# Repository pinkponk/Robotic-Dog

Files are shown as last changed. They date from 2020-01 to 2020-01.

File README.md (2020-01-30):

# Robtic-Dog
A robotic dog capable of walking using 12 robotic servos, an Arduino and a lot of 3D printing. The servos had position feedback and torque control. The onboard arduino mega board talked to the servos through a custom communication curcuit. All the servos used a communication bus which made it possible to daisy chain the communication. The power was drawn from an onboard battery through a dcdc converter to regulate the voltage. It was planned for the robot to use 2 more servos as the spine but there was not enough time to add control code for these 2 servos, the spine was made stiff. The robot did managed to walk but due to the high latency communication, the low resolution position feedback and the time limit it was too difficult to make a dynamic gait work well.

# Documentation
Read the report in the docs dir if you want to know more.

Robot CAD                  |  Target gait
:---------------------------:|:---------------------------------------------:
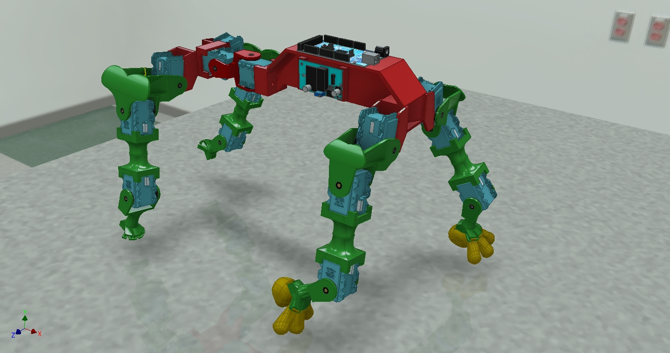
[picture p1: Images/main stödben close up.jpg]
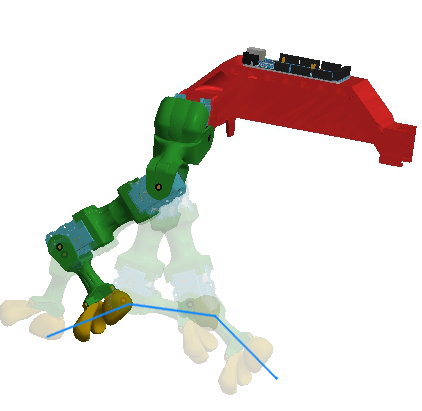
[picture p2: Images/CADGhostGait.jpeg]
  |  

Complete robot                  |  Matlab simulation of gait and inverse kinematics
:---------------------------:|:---------------------------------------------:
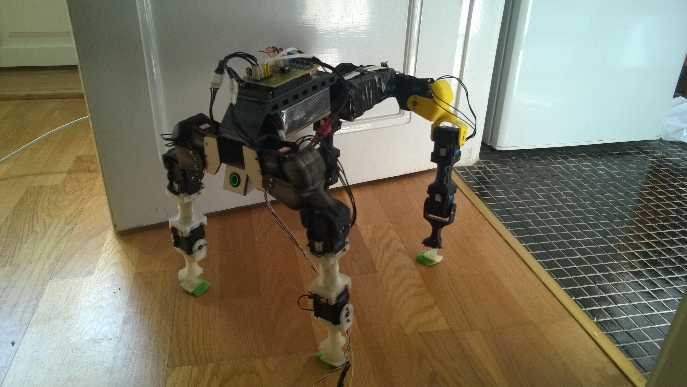
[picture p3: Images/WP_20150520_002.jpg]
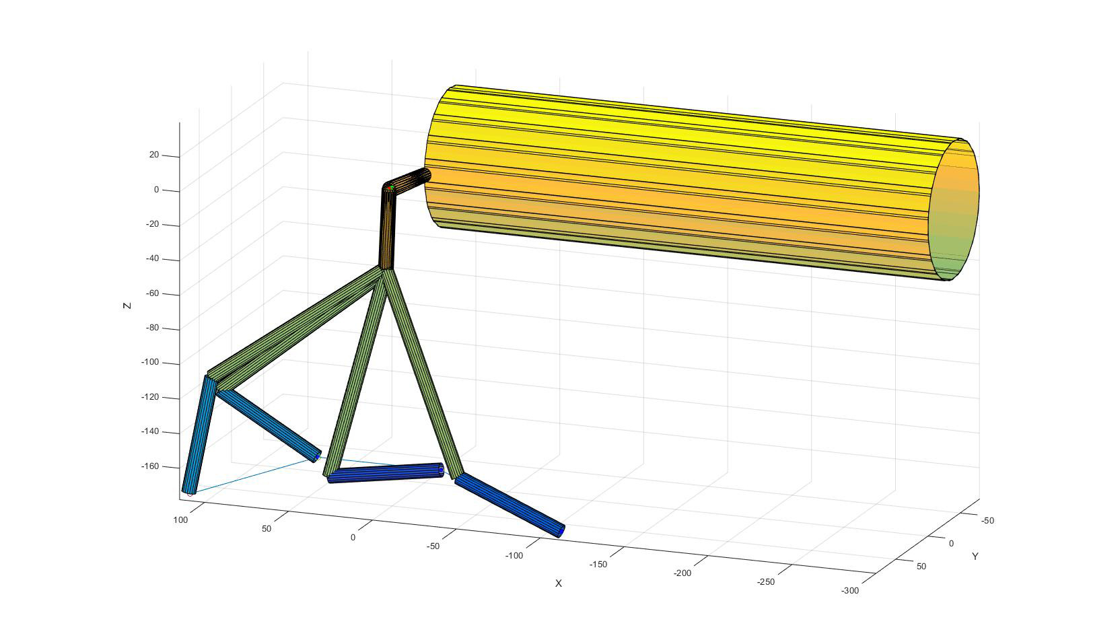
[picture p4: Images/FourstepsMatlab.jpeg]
 | 

Calculating Inverse kinematics                  |  Calculating Inverse kinematics
:---------------------------:|:---------------------------------------------:
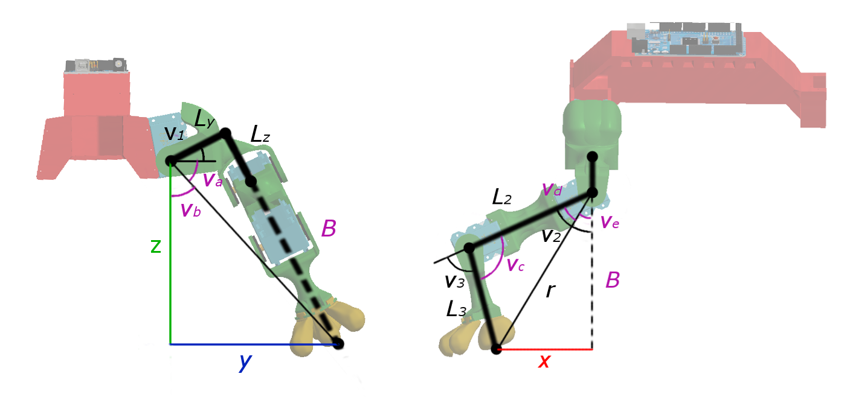
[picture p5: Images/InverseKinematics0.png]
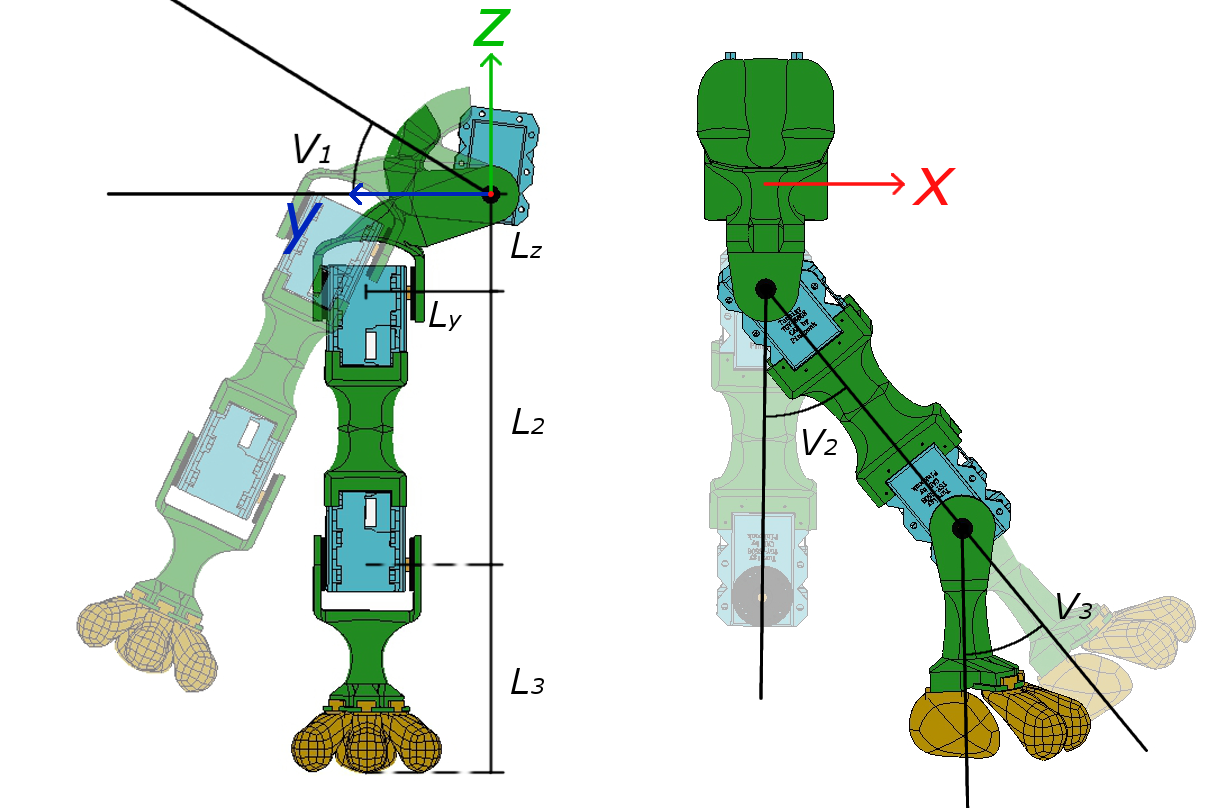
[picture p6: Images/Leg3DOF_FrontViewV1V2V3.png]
  |

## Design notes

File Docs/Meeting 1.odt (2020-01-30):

# Meeting 1

Mitt arbete bygger runt vilket servo jag använder mig av. Jag har beställt ett:

http://hobbyking.com/hobbyking/store/__41216__Turnigy_TGY_S508_300_Digital_Intelligent_Metal_Gear_Robot_Servo_8kg_0_16Sec_75g.html

It has arrived in here in Sweden yesterday so I will begin testing next week. When I actually have the servo and can confirm that it will work with my project I will order the rest. The dimensions given are a bit on the fusy side so I will make the messurment myself when I get the actuall piece. I will probebly have to build some connectors by myself but the majority will be bought, for example like this one:

http://www.ebay.com/itm/131270241221?_trksid=p2055119.m1438.l2649&ssPageName=STRK%3AMEBIDX%3AIT (http://www.ebay.com/itm/131270241221?_trksid=p2055119.m1438.l2649&ssPageName=STRK%3AMEBIDX%3AIT)

I have emailed the buyer I gotten the dimensions needed for this piece but again I will have to check with the actual servo I bought.

To power the servos I will use a battery I already have (12V) I will need some power electronics given that the servos run on 7,6 V. Like this one:

http://www.ebay.com/itm/2PCS-LM317-DC-DC-Converters-Buck-Power-Module-Adjustable-Linear-Regulator-/361095746885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

I will also implement some cheap pressure sensors on each fot, maybe not for a start but later on these will become valuble info:

http://www.ebay.com/itm/0-40kPa-MPS20N0040D-D-DIP-6-Sphygmomanometer-Pressure-Sensor-/331477178244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

Every cool robot needs a sexy power switch:

http://www.ebay.com/itm/16mm-Red-Start-Horn-Button-Momentary-Stainless-Steel-Metal-Push-Button-Switch-/331476329256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

Also some cute eye's:

http://www.ebay.com/itm/MAX7219-Dot-Matrix-Module-Control-Display-Module-DIY-kit-Cascade-uk-/361102115385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

Budget for phase 1:

6 servos = 1284 SEK

6 mounting brackets = 176 SEK

2 DC-DC step down= 24 SEK

2 pressure sensors = 32 SEK

1 power switch = 25 SEK

2 eye's = 52 SEK

Tot = 1600 SEK

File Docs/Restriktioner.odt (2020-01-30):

En motor bör klara av att lyfta halva vikten av roboten => maximal längd för ben

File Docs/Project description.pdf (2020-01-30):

Henrik Ljunggren
2015-02-01

# Quadruped with spine

Project description
I will make a Quadruped, a four legged robot with a spine. The robot will be able to walk using a pre-programmed pattern in phase one and will tech itself how to walk in phase two.

Engineering problem
The foremost problem lays with using ordinary servos. With normal servos no feedback is available and so one never knows the actual location of the leg/arm, making building a walking robot/running robot hard. I will therefore use special servos which can transmit [angle, angle speed, temp and more] back to the controller. These special servos communicate using CAN-bus and are connected in series.

Research question
Phase One: How will a gait with the use of a spine compare with not using a spine? Phase Two: How does a pre-programmed gait/walk compare to a self learned gait/walk?

Components
For phase one I will need, depending on the structural design a lot of special servos around 12-14 and one CAN-bus shield for arduino. I will also need many structural connectors to attach the servos to one and other.
For phase Two I will need som sort of balancing sensor.

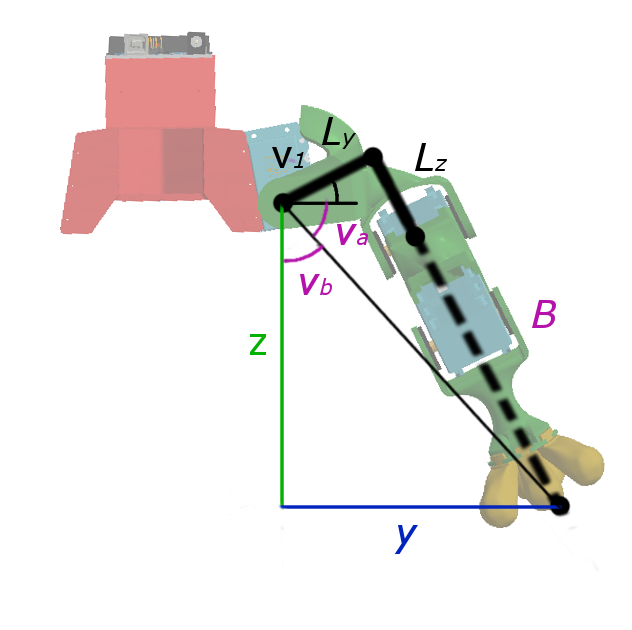
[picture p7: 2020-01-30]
Images/InverseKinematics1.png

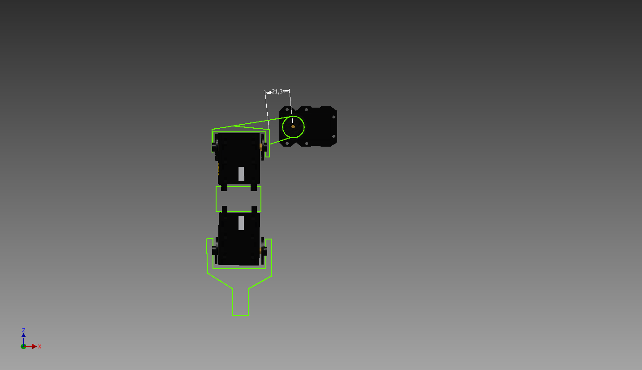
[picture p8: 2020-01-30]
Images/Leg3DOFOverallDesign.bmp

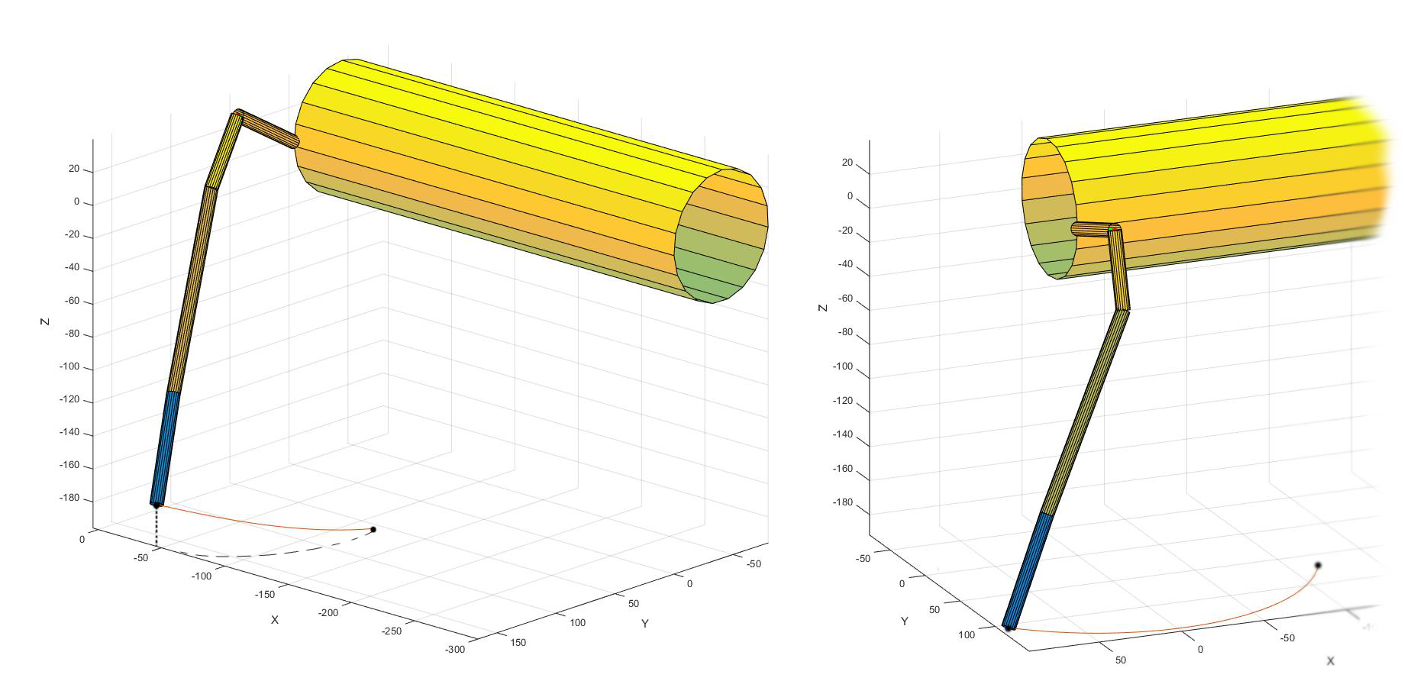
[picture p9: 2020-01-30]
Images/2DoFTransportandSupport.png

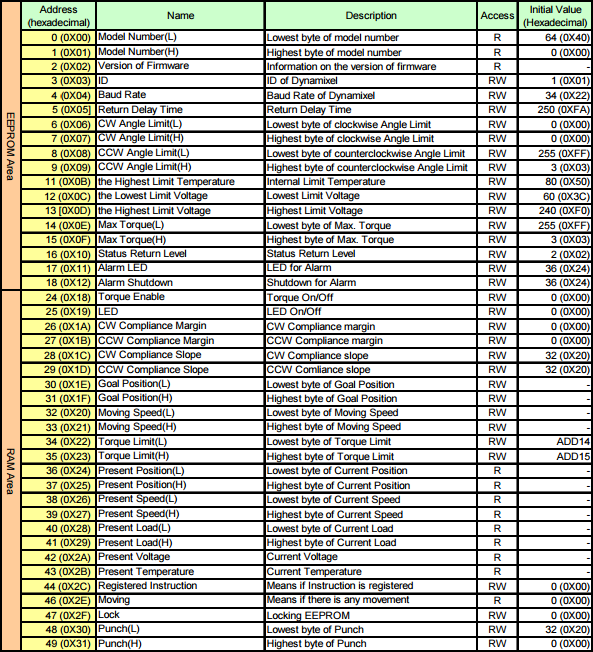
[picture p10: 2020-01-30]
Docs/SR518 servo/ControlTable.png

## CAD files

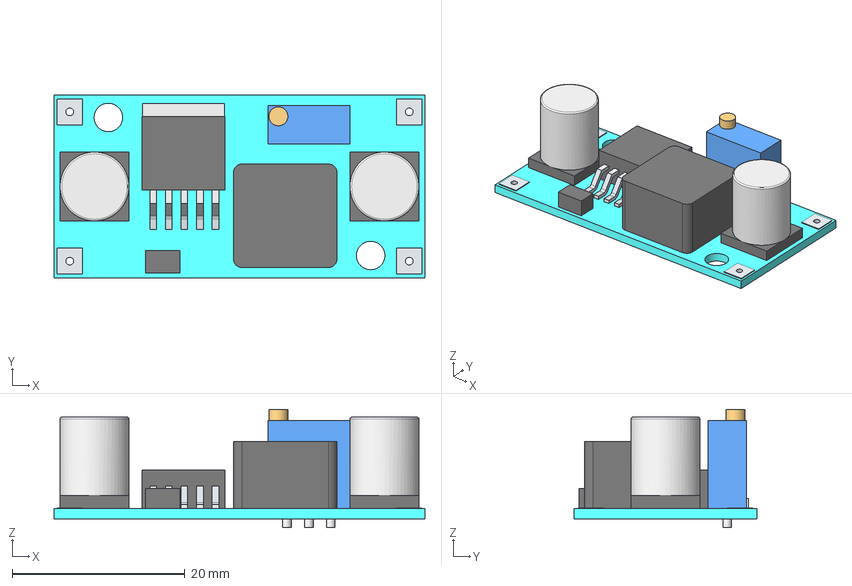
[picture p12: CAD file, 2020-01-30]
CAD/DCDCStepDown/Step Down voltage regulator LM2596.stp
43.0 x 21.2 x 13.7 mm

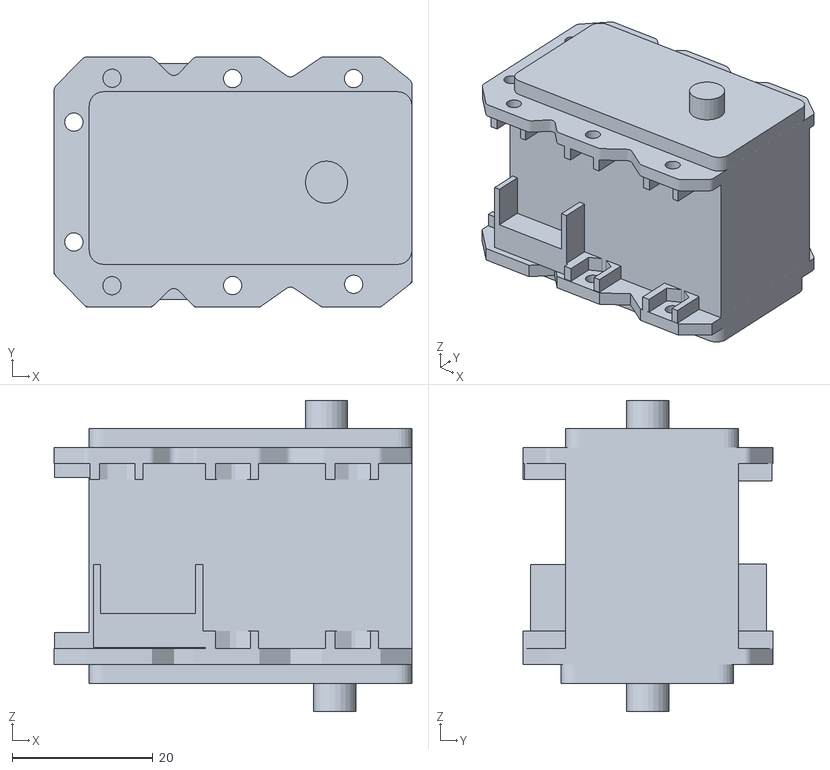
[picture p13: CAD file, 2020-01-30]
Docs/SR518 servo/CAD_SR518 servo/1832732_SR518 servo/SR518 servo.stl
50.8 x 35.5 x 44.1

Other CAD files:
CAD/Arduino Mega 2560/Assembly1.iam
CAD/Arduino Mega 2560/PCB-FIXED.ipt
CAD/Arduino Mega 2560/Part10.ipt
CAD/Arduino Mega 2560/Part12.ipt
CAD/Arduino Mega 2560/Part14.ipt
CAD/Arduino Mega 2560/Part16.ipt
CAD/Arduino Mega 2560/Part18.ipt
CAD/Arduino Mega 2560/Part20.ipt
CAD/Arduino Mega 2560/Part22.ipt
CAD/Arduino Mega 2560/Part24.ipt
CAD/Arduino Mega 2560/Part26.ipt
CAD/Arduino Mega 2560/Part28.ipt
CAD/Arduino Mega 2560/Part30.ipt
CAD/Arduino Mega 2560/Part32.ipt
CAD/Arduino Mega 2560/Part34.ipt
CAD/Arduino Mega 2560/Part36.ipt
CAD/Arduino Mega 2560/Part38.ipt
CAD/Arduino Mega 2560/Part4.ipt
CAD/Arduino Mega 2560/Part40.ipt
CAD/Arduino Mega 2560/Part42.ipt
CAD/Arduino Mega 2560/Part44.ipt
CAD/Arduino Mega 2560/Part46.ipt
CAD/Arduino Mega 2560/Part6.ipt
CAD/Arduino Mega 2560/Part8.ipt
CAD/ButtConnector.ipt
CAD/ChestConnector.ipt
CAD/ChestConnector10Degrees.ipt
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

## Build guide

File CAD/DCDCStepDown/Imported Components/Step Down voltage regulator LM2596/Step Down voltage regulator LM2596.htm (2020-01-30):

Autodesk Inventor Translation Report | den 6 mars 2015 ( 11:03)

Source File: | D:\Study_and_Projects\KTH\KEX i robotik\CAD\DCDCStepDown\Step Down voltage regulator LM2596.stp
Translator Type: | STEP | Sending System: | Unknown
Author: | Unknown | Translation Time: | 00:00:00

Options
Import Type: | N/A
Entity Types to Import: | Solids, Surfaces, Wires, Points
Import into Repair Environment: | Yes
Import Assembly as Single Part: | No
Create Surfaces As: | Single Composite Feature
Units: | millimeter
Check Parts during Load: | No
Auto Stitch: | No
Enable Advanced Healing: | N/A

## Components

The following table lists the parts and assemblies created in Inventor:

+/- | Name | Inventor File | Status
[ ] | Step Down voltage regulator LM2596 | D:\Study_and_Projects\KTH\KEX i robotik\CAD\DCDCStepDown\Imported Components\Step Down voltage regulator LM2596\Step Down voltage regulator LM2596.ipt | Successful

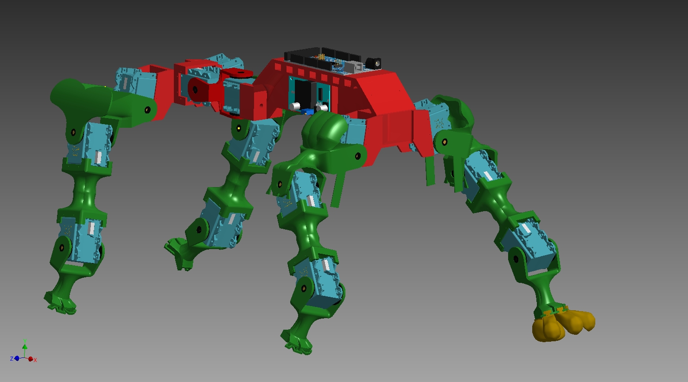
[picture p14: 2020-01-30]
Images/MainAssembly Done.jpg

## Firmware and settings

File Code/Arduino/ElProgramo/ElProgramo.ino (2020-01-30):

//==== Pins   ============   ============
int DEPin = 2; // The pin to be used for enable/disable signal
const int PotPin = 0;
const int sensorPinX = A14;    // select the input pin for the potentiometer
const int sensorPinY = A15;    // select the input pin for the potentiometer
const int buttonPin = 51;      //pin 53 does not work
const int VpwrPin2 = 50;    // select the input pin for the potentiometer

//==== Constants   ============   ============
byte IDAll = 0xFE;

int Ly = 55;  //55,169 mm
int Lz = 45;  //44,856 mm
int L2 = 123; //123,028 mm
int L3 = 67+20;  //67 mm    94,011 mm with heel

float k;
int k_multi = 2;
int state = 3;
int DoF3 = 1;
unsigned long lastPointIncrement;
unsigned long previousSwitchTime;
int timeBetweenPoints; //Millisec
int MaxTimeBetweenPoints = 400;//400; //Millisec
const int nrOfPointsT = 8;
const int nrOfPointsS = nrOfPointsT*3;
const int nrOfPoints = nrOfPointsT+nrOfPointsS;


//===== Input and Control Variables   ============
int buttonState;
int sensorValueX = 0;  // variable to store the value coming from the sensor
int sensorValueY = 0;  // variable to store the value coming from the sensor

//=====   LEG 1   ============ Right Front Leg
byte leg1_3 = 0x01; int leg1_3_dir=1; int leg1_3_offset=-20;
byte leg1_2 = 0x02; int leg1_2_dir=1; int leg1_2_offset=60;
byte leg1_1 = 0x03; int leg1_1_dir=1; int leg1_1_offset=0;
float phaseShift_1 = 0.25;
int currPointIndex_1 = nrOfPoints*phaseShift_1;
int Curve_1[nrOfPoints][3];

int Vspeeds_1[3];
float angleCoord_1[3];
double cartCoord_1[3];

//=====   LEG 2   ============ Left Front Leg
byte leg2_3 = 0x04; int leg2_3_dir=1; int leg2_3_offset=20;
byte leg2_2 = 0x05; int leg2_2_dir=1; int leg2_2_offset=-35;
byte leg2_1 = 0x06; int leg2_1_dir=1; int leg2_1_offset=-30;
float phaseShift_2 = 0.75;
int currPointIndex_2 = nrOfPoints*phaseShift_2;
int Curve_2[nrOfPoints][3] = {0};

int Vspeeds_2[3];
float angleCoord_2[3];
double cartCoord_2[3];

//=====   LEG 3   ============ Right Back Leg
byte leg3_3 = 0x07; int leg3_3_dir=1; int leg3_3_offset=30;
byte leg3_2 = 0x08; int leg3_2_dir=1; int leg3_2_offset=-30;
byte leg3_1 = 0x09; int leg3_1_dir=1; int leg3_1_offset=40;
float phaseShift_3 = 0;
int currPointIndex_3 = nrOfPoints*phaseShift_3;
int Curve_3[nrOfPoints][3] = {0};

int Vspeeds_3[3];
float angleCoord_3[3];
double cartCoord_3[3];

//=====   LEG 4   ============ Left Back Leg
byte leg4_3 = 10; int leg4_3_dir=1; int leg4_3_offset=0;
byte leg4_2 = 11; int leg4_2_dir=1; int leg4_2_offset=-15;
byte leg4_1 = 12; int leg4_1_dir=1; int leg4_1_offset=-15;
float phaseShift_4 = 0.5;
int currPointIndex_4 = nrOfPoints*phaseShift_4;
int Curve_4[nrOfPoints][3] = {0};

int Vspeeds_4[3];
float angleCoord_4[3];
double cartCoord_4[3];


//==== Temp and Log Variables   ============   ============
int i=0;
int powerConsumpiton[10] ={0};
byte sendingData[10];
byte returningData[20];
int corupptReturnData=0;



void setup() {
  Serial2.begin(500000);
  Serial.begin(19200);
  pinMode(VpwrPin2, OUTPUT);
  pinMode(buttonPin, INPUT_PULLUP);    //Pull up
  digitalWrite(VpwrPin2, HIGH);
  
  pinMode(DEPin, OUTPUT);
  digitalWrite(DEPin,LOW);
  
  //makeCurve(Curve_1, 1, -1, -1, 1);
  //makeCurve(Curve_2);
  limitReturnPackage(IDAll,1);
  setDelayTime(IDAll,10);      //A value of 100 sets the delay time to 200microsek
  setMaxTorque(IDAll,1023);      //To try to solve the pwr problem
  delay(8);              //PWR PROBLEM Need this in order for all the servos to actually move to 512, don't not yet why but could have to do with power to the servos or the command above
   moveServo (IDAll, 512);
   delay(80);

  
  previousSwitchTime=millis();
  lastPointIncrement = millis();
}

void loop() {
  int valPot;
  int xtarget_1;
  int ytarget_1;
  int ztarget_1;
  
  int xtarget_2;
  int ytarget_2;
  int ztarget_2;
  
  int xtarget_3;
  int ytarget_3;
  int ztarget_3;
  
  int xtarget_4;
  int ytarget_4;
  int ztarget_4;
  float turn;
  

  switch(state){
    case 1:
    delay(10);
      buttonState = digitalRead(buttonPin);
      valPot = analogRead(PotPin);    // read the input pin
      k = map(valPot, 0, 1023, 0, 200*k_multi)/100.0;
      sensorValueX = analogRead(sensorPinX);
      sensorValueY = analogRead(sensorPinY);
      timeBetweenPoints = map(sensorValueX, 0, 1023, 0, MaxTimeBetweenPoints);
      turn = map(sensorValueY, 0, 1023, -100, 100)/100.0;
      
       if (buttonState==LOW && (millis()-previousSwitchTime)>100){
        DoF3 = (DoF3+1)%2;
        previousSwitchTime = millis();
       }
      
      makeCurve(Curve_1, abs(turn), sign(((int)(turn*100))), 1,DoF3);
      makeCurve(Curve_2, abs(turn), sign(((int)(turn*100))), -1,DoF3);
      
      makeCurve(Curve_3, abs(turn), sign(((int)(turn*100))), 1,DoF3);
      makeCurve(Curve_4, abs(turn), sign(((int)(turn*100))), -1,DoF3);
      
      timeSyncNextPoint();

//        Serial.write(27);       // ESC command
//        Serial.print("[2J");    // clear screen command
//        Serial.write(27);
//        Serial.print("[H");     // cursor to home command
//      Serial.print("CurrPoint=");Serial.println(currPointIndex_1);
//      Serial.print("sensorValueY=");Serial.println(sensorValueY);
//      Serial.print("timeBetweenPoints=");Serial.println(timeBetweenPoints);
//      Serial.print("Load ID 2=");Serial.println(getLoad(2));
//      printInfo(1);
      
      //========LEG 1=========
      xtarget_1 = Curve_1[currPointIndex_1%nrOfPoints][0];
      ytarget_1 = Curve_1[currPointIndex_1%nrOfPoints][1];
      ztarget_1 = Curve_1[currPointIndex_1%nrOfPoints][2];
      
//      InverseKinematics(xtarget_1, ytarget_1, ztarget_1,angleCoord_1);
//      moveServo (leg1_1, convertToServoAngle(angleCoord_1[0])+leg1_1_offset);
//      moveServo (leg1_2, convertToServoAngle(angleCoord_1[1])+leg1_2_offset);
//      moveServo (leg1_3, convertToServoAngle(angleCoord_1[2])+leg1_3_offset);

      
      calcNewSpeeds(xtarget_1,ytarget_1,ztarget_1,leg1_1,leg1_2,leg1_3,Vspeeds_1, angleCoord_1,1,  leg1_1_offset, leg1_2_offset, leg1_3_offset);
      prepareSpeed(leg1_1, Vspeeds_1[0]*leg1_1_dir);
      prepareSpeed(leg1_2, Vspeeds_1[1]*leg1_2_dir);
      prepareSpeed(leg1_3, Vspeeds_1[2]*leg1_3_dir);

      
      //========LEG 2=========      
      xtarget_2 = Curve_2[currPointIndex_2%nrOfPoints][0];
      ytarget_2 = Curve_2[currPointIndex_2%nrOfPoints][1];
      ztarget_2 = Curve_2[currPointIndex_2%nrOfPoints][2];
      
//      InverseKinematics(xtarget_2, ytarget_2, ztarget_2,angleCoord_2);
//      moveServo (leg2_1, convertToServoAngle(angleCoord_2[0])+leg2_1_offset);
//      moveServo (leg2_2, convertToServoAngle(angleCoord_2[1])+leg2_2_offset);
//      moveServo (leg2_3, convertToServoAngle(angleCoord_2[2])+leg2_3_offset);
      
      calcNewSpeeds(xtarget_2,ytarget_2,ztarget_2,leg2_1,leg2_2,leg2_3,Vspeeds_2, angleCoord_2,-1,  leg2_1_offset, leg2_2_offset, leg2_3_offset);
      prepareSpeed(leg2_1, Vspeeds_2[0]*leg2_1_dir);
      prepareSpeed(leg2_2, Vspeeds_2[1]*leg2_2_dir);
      prepareSpeed(leg2_3, Vspeeds_2[2]*leg2_3_dir);
      
      //========LEG 3=========      
      xtarget_3 = Curve_3[currPointIndex_3%nrOfPoints][0];
      ytarget_3 = Curve_3[currPointIndex_3%nrOfPoints][1];
      ztarget_3 = Curve_3[currPointIndex_3%nrOfPoints][2];
      
//      InverseKinematics(xtarget_3, ytarget_3, ztarget_3,angleCoord_3);
//      moveServo (leg3_1, convertToServoAngle(angleCoord_3[0])+leg3_1_offset);
//      moveServo (leg3_2, convertToServoAngle(angleCoord_3[1])+leg3_2_offset);
//      moveServo (leg3_3, convertToServoAngle(angleCoord_3[2])+leg3_3_offset);
      
      calcNewSpeeds(xtarget_3,ytarget_3,ztarget_3,leg3_1,leg3_2,leg3_3,Vspeeds_3, angleCoord_3,1,  leg3_1_offset, leg3_2_offset, leg3_3_offset);
      prepareSpeed(leg3_1, Vspeeds_3[0]*leg3_1_dir);
      prepareSpeed(leg3_2, Vspeeds_3[1]*leg3_2_dir);
      prepareSpeed(leg3_3, Vspeeds_3[2]*leg3_3_dir);
      
      //========LEG 4=========      
      xtarget_4 = Curve_4[currPointIndex_4%nrOfPoints][0];
      ytarget_4 = Curve_4[currPointIndex_4%nrOfPoints][1];
      ztarget_4 = Curve_4[currPointIndex_4%nrOfPoints][2];
      
//      InverseKinematics(xtarget_4, ytarget_4, ztarget_4,angleCoord_4);
//      moveServo (leg4_1, convertToServoAngle(angleCoord_4[0])+leg4_1_offset);
//      moveServo (leg4_2, convertToServoAngle(angleCoord_4[1])+leg4_2_offset);
//      moveServo (leg4_3, convertToServoAngle(angleCoord_4[2])+leg4_3_offset);
      
      calcNewSpeeds(xtarget_4,ytarget_4,ztarget_4,leg4_1,leg4_2,leg4_3,Vspeeds_4, angleCoord_4,-1,  leg4_1_offset, leg4_2_offset, leg4_3_offset);
      prepareSpeed(leg4_1, Vspeeds_4[0]*leg4_1_dir);
      prepareSpeed(leg4_2, Vspeeds_4[1]*leg4_2_dir);
      prepareSpeed(leg4_3, Vspeeds_4[2]*leg4_3_dir);
      
      //====ACTIVATE====
      activateSpeeds();
      
      
      
//      Serial.println("%%%%%%%%%%%%%%%%%%%%%%");
////      printInfo(1);
//      Serial.print("valPot=");Serial.print(valPot);
//      Serial.print("  k=");printFloat(k, 3);
//      Serial.print("  currPointIndex=");Serial.println(currPointIndex_1);
//
//      
//                  Serial.print("   xtarget=");Serial.print(xtarget_1);
//                  Serial.print("         ytarget=");Serial.print(ytarget_1);
//                  Serial.print("            ztarget=");Serial.println(ztarget_1);        //FEL I UTRÄKNADE KORDINATERNA <-vet inte längre
////            
////
////      
////      
////
//                  Serial.print("v1Speed=");Serial.println(Vspeeds_1[0]);
//                  Serial.print("v2Speed=");Serial.println(Vspeeds_1[1]);
//                  Serial.print("v3Speed=");Serial.println(Vspeeds_1[2]);
      
  
  
      break;
    
    case 3:
        delay(50);
        goToZero();
      if (digitalRead(6)){
        state=1;
        lastPointIncrement = millis();
        }
      break;
    }
  
}

void goToZero(){
  

  moveServo(leg1_1, 512+leg1_1_offset);
  moveServo(leg1_2, 512+leg1_2_offset);
  moveServo(leg1_3, 512+leg1_3_offset);
  
  moveServo(leg2_1, 512+leg2_1_offset);
  moveServo(leg2_2, 512+leg2_2_offset);
  moveServo(leg2_3, 512+leg2_3_offset);
  
  moveServo(leg3_1, 512+leg3_1_offset);
  moveServo(leg3_2, 512+leg3_2_offset);
  moveServo(leg3_3, 512+leg3_3_offset);
  
  moveServo(leg4_1, 512+leg4_1_offset);
  moveServo(leg4_2, 512+leg4_2_offset);
  moveServo(leg4_3, 512+leg4_3_offset);
  
  
  
  }

void timeSyncNextPoint(){
  int timeDelay = (timeBetweenPoints-(millis()-lastPointIncrement));
  if (timeDelay<=0){
      currPointIndex_1++;
      currPointIndex_2++;
      currPointIndex_3++;
      currPointIndex_4++;
      //(*PointIndexPointer)++;    //(*PointIndexPointer)++; The parantasis are most vital otherwise the pointer will be ++ first
      //getLoad(1);
      
//      powerConsumpiton[i%10]=0;
//      for (int ii = 1; ii < 5; ii++) {
//      powerConsumpiton[i%10] = powerConsumpiton[i%10]+getLoad(ii)%1023;
//       delay(1);     
//    }
//      int meanPwr=0;
//      for (int ii = 0; ii < 10; ii++) {
//       meanPwr = meanPwr+powerConsumpiton[ii]/5;
//       } 
//      Serial.print("pwrcons=");Serial.println(meanPwr/10);
//      i++;
      
      lastPointIncrement=millis();
   }
}

void printInfo(int leg){
  
  
  Serial.print("showing info for leg=");
  Serial.println(leg);
  for (int i=1; i <= 3; i++){
  int ID = i+(leg-1)*3;
  Serial.println("=================");
  int pos = getCurrPos(ID);
  int Speed = getCurrSpeed(ID);
  int SpeedValue = Speed&1023;
  int SpeedDir = Speed>>10;
  Serial.print("ID=");Serial.print(ID);
  Serial.print("  Pos=");Serial.print(pos);
  Serial.print("  Speed=");Serial.print(SpeedValue);Serial.print("  SpeedDir=");Serial.print(SpeedDir);
  Serial.print("  Voltage=");Serial.print(getVoltage(ID));
  Serial.print("  CCWLimit=");Serial.print(getCCWLimit(ID)); Serial.print("  CWLimit=");Serial.println(getCWLimit(ID));    
  
  }
  Serial.println("=================");
  }


int convertToServoAngle(float radAngle){
  //WORKS
 return map(radAngle*1000, -2.618*1000, 2.618*1000, 0, 1023);    //2.618=150*PI/180
  }


float convertFromServoAngle(int bitAngle){
  //WORKS
 return map(bitAngle, 0, 1023, -2.618*1000, 2.618*1000)/1000.0;  //2.618=150*PI/180
  }


void calcNewSpeeds(int xtarget,int ytarget,int ztarget,int IDv1,int IDv2,int IDv3, int Vspeeds[3], float* angleCoord, int leftOrRight, int leg_1_offset, int leg_2_offset, int leg_3_offset){
  //leftOrRight [-1 | 1], -1=left, 1=right
  
  
  int v1Pos = getCurrPos(IDv1)-leg_1_offset;if(corupptReturnData==1){return;}
  int v2Pos = getCurrPos(IDv2)-leg_2_offset;if(corupptReturnData==1){return;}
  int v3Pos = getCurrPos(IDv3)-leg_3_offset;if(corupptReturnData==1){return;}
  
  float v1Curr = convertFromServoAngle(v1Pos)*leftOrRight;
  float v2Curr = convertFromServoAngle(v2Pos)*leftOrRight;
  float v3Curr = convertFromServoAngle(v3Pos)*leftOrRight;
//  Serial.print("deg v1Curr=");printFloat(v1Curr*180/PI, 3);
//  Serial.print("    deg v2Curr=");printFloat(v2Curr*180/PI, 3);
//  Serial.print("    deg v3Curr=");printFloat(v3Curr*180/PI, 3);Serial.println();  
  
  InverseKinematics(xtarget, ytarget, ztarget, angleCoord);
  float dv1 = angleCoord[0]-v1Curr;    //Still in Radians
  float dv2 = angleCoord[1]-v2Curr;
  float dv3 = angleCoord[2]-v3Curr;
//  Serial.print("deg target v1=");printFloat(convertToServoAngle(angleCoord[0]), 3);
//  Serial.print("    deg target v2=");printFloat(convertToServoAngle(angleCoord[1]), 3);
//  Serial.print("    deg target v3=");printFloat(convertToServoAngle(angleCoord[2]), 3);Serial.println();
//  
//  Serial.print("   deg dv1=");printFloat(dv1*180/PI, 3);
//  Serial.print("        deg dv2=");printFloat(dv2*180/PI, 3);
//  Serial.print("        deg dv3=");printFloat(dv3*180/PI, 3);Serial.println();

  
  int v1Speed = map( dv1*1000,(-PI/2.0)*1000,(PI/2.0)*1000, -1023, 1023)*k*leftOrRight;    //Value can get higher than 1023 if the angle difference is bugger than pi/4
  int v2Speed = map( dv2*1000,(-PI/2.0)*1000,(PI/2.0)*1000, -1023, 1023)*k*leftOrRight;    //Value can get higher than 1023 if the angle difference is bugger than pi/4
  int v3Speed = map( dv3*1000,(-PI/2.0)*1000,(PI/2.0)*1000, -1023, 1023)*k*leftOrRight;    //Value can get higher than 1023 if the angle difference is bugger than pi/4

//  Serial.print("   v1Speed=");printFloat(v1Speed, 3);
//  Serial.print("        v1Speed=");printFloat(v2Speed, 3);
//  Serial.print("        v1Speed=");printFloat(v3Speed, 3);Serial.println();


//  int v1Speed = dv1*k;
//  int v2Speed = dv2*k;
//  int v3Speed = dv3*k;
  
  Vspeeds[0] = v1Speed;Vspeeds[1] = v2Speed;Vspeeds[2] = v3Speed;
  }



void makeCurve(int curve[][3], float turn, int turningLeftOrRight, int leftOrRightLeg, int DoF3){
  //turn = [0->1], how much you want to turn
  //turningLeftOrRight = [-1 | 1], -1 = turn left, 1 = turn right
  //leftOrRightLeg = [-1 | 1], -1 = left leg, 1 = right leg
  
  
  if (DoF3 == 1){
    
  //3 DOF LEG MOTION
//  int startXtransport = -110;
//  int endXtransport = 110;
  int startXtransport = -60;
  int endXtransport = 60;
  int yOffsetTurn = 60*turn*turningLeftOrRight*leftOrRightLeg;
  float stepSizeX = (endXtransport-startXtransport)/(nrOfPoints/4.0-1);
  float stepSizeY = (yOffsetTurn-0)/(nrOfPoints/4.0-1);
  
   for (int i=0; i < (nrOfPoints/4); i++){
    curve[i][0]=startXtransport+stepSizeX*i;
//    curve[i][1]=60-pow((curve[i][0]/40),2)+8+stepSizeY*i-yOffsetTurn/2;    //added this remember that, 21:34
//    curve[i][2]=-145-pow((curve[i][0]/20.0),2);
    curve[i][1]=0+stepSizeY*i-yOffsetTurn/2;    //added this remember that, 21:34 -34 = very close feet
    curve[i][2]=-115-70-0-pow(((curve[i][0]-0)/8.0),2);
  }
  
  stepSizeX = (startXtransport-endXtransport)/(nrOfPoints/(3/4.0)-1);
  stepSizeY = (curve[0][1]-curve[nrOfPoints/4-1][1])/(nrOfPoints/(3/4.0)-1);
  int z = curve[0][2];
  
    for (int i=nrOfPoints/4; i < (nrOfPoints); i++){
    curve[i][0]=curve[nrOfPoints/4-1][0]+stepSizeX*(i-nrOfPoints/4);
    curve[i][1]=curve[nrOfPoints/4-1][1]+stepSizeY*(i-nrOfPoints/4);
    curve[i][2]=z;
  }
  }else{
    
    
  //2 DOF LEG MOTION
  //int xOffsetTurn = turn*turningLeftOrRight*leftOrRightLeg;        //Turning is done by offsetting the x so that an offset in y is created
  int startXtransport = -60;//-xOffsetTurn*10;
  int endXtransport = 60;//-xOffsetTurn*10;
  float stepSizeX = (endXtransport-startXtransport)/(nrOfPoints/2.0-1);
  
   for (int i=0; i < (nrOfPoints/2); i++){
    curve[i][0]=startXtransport+stepSizeX*i;    //x
    curve[i][2]=-218-pow((curve[i][0]/10.0),2);  //z
    curve[i][1]=sqrt(pow(Ly,2)+pow((sqrt(pow((L2+L3),2)-pow(curve[i][0],2))+Lz),2)-pow(curve[i][2],2))-1;    //The one is for not getting imaginary when inverse kinematics

  }
  
  stepSizeX = (startXtransport-endXtransport)/(nrOfPoints/2.0-1);
  int z = curve[0][2];
  
    for (int i=nrOfPoints/2; i < (nrOfPoints); i++){
    curve[i][0]=curve[nrOfPoints/2-1][0]+stepSizeX*(i-nrOfPoints/2);
    curve[i][1]=-(sqrt(pow(Ly,2)+pow((sqrt(pow((L2+L3),2)-pow(curve[i][0],2))+Lz),2)-pow(curve[i][2],2))-1);    //The one is for not getting imaginary when inverse kinematics
    //curve[i][2]=z;
    curve[i][2]=-253;
  }   
    
    
    }
  
}






void InverseKinematics(double x, double y, double z, float* angleCoords){
  
  float v1 = (atan(y/abs(z))+acos(Ly/sqrt(pow(z,2)+pow(y,2))))-PI/2;

  double x1 = 0;
  double y1 = Ly*cos(v1)+Lz*sin(v1);
  double z1 = Ly*sin(v1)-Lz*cos(v1);
  
  double r = sqrt(pow((x1-x),2)+pow((y1-y),2)+pow((z1-z),2));
  float v3 = PI-acos((pow(L2,2)+pow(L3,2)-pow(r,2))/(2*L2*L3));
  
  double B = abs(z-z1);
  float beta = atan(x/B/cos(v1));
  float v2 = acos((pow(r,2)+pow(L2,2)-pow(L3,2))/(2*r*L2))+beta;
  
  angleCoords[0]=v1;angleCoords[1]=v2;angleCoords[2]=v3;
  }


void Forwardkinematics(float v1,float v2,float v3, double* cartCoords){
  //Angles in Radians!
  
//  int x1 = 0;
//  int y1 = Ly*cosd(v1);
//  int z1 = Ly*sind(v1);
//  
//  int x2 = 0;
//  int y2 = y1+Lz*sind(v1);
//  int z2 = z1-Lz*cosd(v1);
//  
//  int x3 = L2*sind(v2);
//  int y3 = y2+L2*cosd(v2)*sind(v1);
//  int z3 = z2-L2*cosd(v2)*cosd(v1);
// 
//  int x4 = x3+L3*sind(v2-v3);
//  int y4 = y3+L3*cosd(v2-v3)*sind(v1);
//  int z4 = z3-L3*cosd(v2-v3)*cosd(v1);
  
  double x = double (L2*sin(v2)+L3*sin(v2-v3));
  double y = double (Ly*cos(v1)+Lz*sin(v1)+L2*cos(v2)*sin(v1)+L3*cos(v2-v3)*sin(v1));
  double z = double (Ly*sin(v1)-Lz*cos(v1)-L2*cos(v2)*cos(v1)-L3*cos(v2-v3)*cos(v1));

  cartCoords[0]=x;cartCoords[1]=y;cartCoords[2]=z;
 }


//==================================
//==================================
//==================================
//           GETS and SETS

void setIDtoAll(int value){
  //if(checkIsBetweenValue(value,0, 1)){
  byte buf[] = {0xFE,0x04,0x03,0x03,value};
  memcpy ( sendingData, buf, sizeof(buf) );  //sizeof(buf)
  sendInformation(sendingData, sizeof(buf));
  //}
}


void limitReturnPackage(byte ID, int value){
  byte buf[] = {ID,0x04,0x03,0x10,value};
  memcpy ( sendingData, buf, sizeof(buf) );  //sizeof(buf)
  sendInformation(sendingData, sizeof(buf));
  }


int getCurrPos(byte ID){
  byte buf[] = {ID,0x04,0x02,0x24,0x02};
  memcpy ( sendingData, buf, sizeof(buf) );  //sizeof(buf)
  sendInformation(sendingData, sizeof(buf));
  getInfo();
  return (returningData[5]+returningData[6]*255);
  }


int getCurrSpeed(byte ID){
  byte buf[] = {ID,0x04,0x02,0x26,0x02};
  memcpy ( sendingData, buf, sizeof(buf) );  //sizeof(buf)
  sendInformation(sendingData, sizeof(buf));
  getInfo();
  return ((returningData[5]+returningData[6]*255));
  }
  
int getSetSpeed(byte ID){
  byte buf[] = {ID,0x04,0x02,0x20,0x02};
  memcpy ( sendingData, buf, sizeof(buf) );  //sizeof(buf)
  sendInformation(sendingData, sizeof(buf));
  getInfo();
  return ((returningData[5]+returningData[6]*255));
  }
  
int getIsMoving(byte ID){
  byte buf[] = {ID,0x04,0x02,0x2E,0x01};
  memcpy ( sendingData, buf, sizeof(buf) );  //sizeof(buf)
  sendInformation(sendingData, sizeof(buf));
  getInfo();
  return (returningData[5]);
  }
  
int getEnableTorque(byte ID){
  byte buf[] = {ID,0x04,0x02,0x18,0x01};
  memcpy ( sendingData, buf, sizeof(buf) );  //sizeof(buf)
  sendInformation(sendingData, sizeof(buf));
  getInfo();
  return (returningData[5]);
  }

void setEnableTorque(byte ID,int value){
  //if(checkIsBetweenValue(value,0, 1)){
  byte buf[] = {ID,0x04,0x03,0x18,value};
  memcpy ( sendingData, buf, sizeof(buf) );  //sizeof(buf)
  sendInformation(sendingData, sizeof(buf));
  //}
}

void setMaxTorque(byte ID,int value){
  if(checkIsBetweenValue(value,0, 1023)){
  byte buf[] = {ID,0x05,0x03,0x0E,lowByte(value),highByte(value)};
  memcpy ( sendingData, buf, sizeof(buf) );  //sizeof(buf)
  sendInformation(sendingData, sizeof(buf));
  }else{
    Serial.print("Error in setMaxTorque");}
}


int getDelayTime(byte ID){
  byte buf[] = {ID,0x04,0x02,0x05,0x01};
  memcpy ( sendingData, buf, sizeof(buf) );  //sizeof(buf)
  sendInformation(sendingData, sizeof(buf));
  getInfo();
  return (returningData[5]);
  }
  
void setDelayTime(byte ID,int value){
  if(checkIsBetweenValue(value,0, 250)){
  byte buf[] = {ID,0x04,0x03,0x05,value};
  memcpy ( sendingData, buf, sizeof(buf) );  //sizeof(buf)
  sendInformation(sendingData, sizeof(buf));
  }
}
  
int getVoltage(byte ID){
  byte buf[] = {ID,0x04,0x02,0x2A,0x01};
  memcpy ( sendingData, buf, sizeof(buf) );  //sizeof(buf)
  sendInformation(sendingData, sizeof(buf));
  getInfo();
  return (returningData[5]);
  }
  
int getTemp(byte ID){
  byte buf[] = {ID,0x04,0x02,0x2B,0x01};
  memcpy ( sendingData, buf, sizeof(buf) );  //sizeof(buf)
  sendInformation(sendingData, sizeof(buf));
  getInfo();
  return (returningData[5]);
  }
  
int getStatusLvl(byte ID){
  byte buf[] = {ID,0x04,0x02,0x10,0x01};
  memcpy ( sendingData, buf, sizeof(buf) );  //sizeof(buf)
  sendInformation(sendingData, sizeof(buf));
  getInfo();
  return (returningData[5]);
}
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

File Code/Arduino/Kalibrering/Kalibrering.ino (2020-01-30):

int state = 1;
int CCW_IDP_button = -1;
int CW_IDM_button = -1;
int freerunbutton = -1;
int resetAnglebutton = -1;
int movePotbutton = -1;
int currID = 1;
int valPot = 512;
const int CCW_IDP_buttonPin = 3;
const int CW_IDM_buttonPin = 4;
const int freerunbuttonPin = 5;
const int resetAnglebuttonPin = 6;
const int movePotbuttonPin = 7;
const int PotPin = 0;
const int DEPin = 2; // The pin to be used for enable/disable signal

byte sendingData[10];
byte returningData[20];

void setup() {
   pinMode(CCW_IDP_buttonPin, INPUT);
   pinMode(CW_IDM_buttonPin, INPUT);
   pinMode(freerunbuttonPin, INPUT);
   pinMode(resetAnglebuttonPin, INPUT);
   pinMode(movePotbuttonPin, INPUT);
   pinMode(DEPin, OUTPUT);
   Serial2.begin(500000);
   Serial.begin(19200);
   delay(1000);

   lightServo(0xFE,1);
   delay(1000);
   limitReturnPackage(0xFE,1);
//   delay(1000);
   setDelayTime(0xFE,10);      //A value of 100 sets the delay time to 200microsek
//   delay(1000);
//   freeRun(false);
//   delay(1000);
   

}

void loop() {
  
  CCW_IDP_button = digitalRead(CCW_IDP_buttonPin);
  CW_IDM_button = digitalRead(CW_IDM_buttonPin);
  freerunbutton = digitalRead(freerunbuttonPin);
  resetAnglebutton = digitalRead(resetAnglebuttonPin);
  movePotbutton = digitalRead(movePotbuttonPin);
  valPot = analogRead(PotPin);    // read the input pin
  
  switch(state){
    case 1:
    //Move with Pot
      delay(10);
      moveServo(currID,valPot);
      
      if (resetAnglebutton==1){
        state = 2;
        
      }else if(freerunbutton==1){
        state = 3;
        
      }else if(CCW_IDP_button==1 && CW_IDM_button==1){
        setCCWLimit(1023);
        setCWLimit(0);
        delay(300);
    
      }else if(CCW_IDP_button==1){
        //setCCWLimit(getCurrPos());
        //setEnableTorque(1);
       // setTorqueLimit(10);
        delay(300);
    
      }else if(CW_IDM_button==1){
        //setCWLimit(getCurrPos());
        //setEnableTorque(0);
        delay(300);
      } 
      
      break;
    case 2:
    //Go to middle, 150 degrees, change currID, reset ID currID to all servos connected
    delay(10);
    moveServo(currID,512);

    if (movePotbutton==1){
      state = 1;
      
    }else if(freerunbutton==1){
      state = 3;
      
    }else if(CCW_IDP_button==1 && CW_IDM_button==1){
      //Dont fuck up
      setIDtoAll(currID);
      lightServo(currID,0);
      delay(100);
      lightServo(currID,1);
      delay(100);
      lightServo(currID,0);
      delay(100);
      lightServo(currID,1);
      delay(100);

  
    }else if(CCW_IDP_button==1){
      lightServo(currID,0);
      currID++;
      lightServo(currID,1);
      delay(300);
  
    }else if(CW_IDM_button==1){
      lightServo(currID,0);
      currID--;
      lightServo(currID,1);
      delay(300);
    } 
    
    break;
    case 3:
    //Freerun CW and CCW
    delay(1);
    
    if (movePotbutton==1){
      state = 1;
      
    }else if(resetAnglebutton==1){
      state = 2;
      
    }else if(CCW_IDP_button==1){

//      freeRun(true);
//      delay(2);
//      freeRunActivate(1);
//      delay(2);
  
    }else if(CW_IDM_button==1){

//      freeRun(true);
//      delay(2);
//      freeRunActivate(0);
//      delay(2);
     
      
    }else{
      
//      freeRun(false);
//      delay(2);
//
//      setSpeed1(0,0);
//      delay(2);
      }
    
    
    break;
     
  }
      printAllInfo2Serial();
      delay(1);
}














void printAllInfo2Serial(){
    

    Serial.write(27);       // ESC command
    Serial.print("[2J");    // clear screen command
    Serial.write(27);
    Serial.print("[H");     // cursor to home command
  
    Serial.print("Servo ID=");
    Serial.print(currID);
    Serial.print("     State=");
    Serial.println(state);
    Serial.print("AnalogPot =");
    Serial.println(valPot);
    Serial.print("Position =");
    Serial.println(getCurrPos());
    int Speed = getCurrSpeed();
    Serial.print("Speed= ");
    Serial.print(Speed&1023);  //Keeps the first 10 bits by using and with binary number 1111111111 (1023)
    Serial.print("    Dir=");
    Serial.print(Speed>>10);
    int Speed2 = getSetSpeed();
    Serial.print("  ||  Target Speed= ");
    Serial.print(Speed2&1023);  //Keeps the first 10 bits by using and with binary number 1111111111 (1023)
    Serial.print("    Dir=");
    Serial.println(Speed2>>10);
    Serial.print("IsMoving=");
    Serial.println(getIsMoving());
    Serial.print("Temp=");
    Serial.println(getTemp());
    Serial.print("Voltage=");
    Serial.println(getVoltage());
    Serial.print("CCWLimit=");
    Serial.print(getCCWLimit());
    Serial.print("  ||  CWLimit=");
    Serial.println(getCWLimit());
    
    Serial.print("Load=");
    int load = getLoad();
    Serial.print(load&1023);  //Load does not read right
    Serial.print("    Dir=");
    Serial.println(load>>10);
    Serial.print("Return Delay Time=");
    Serial.println(getDelayTime());
    Serial.print("Torque Enabled=");
    Serial.println(getEnableTorque());
    Serial.print("Status LVL=");
    Serial.println(getStatusLvl());
    Serial.print("ping error=");
    Serial.println(ping(currID));
    Serial.print("TorqueLimit=");
    Serial.println(getTorqueLimit());
    
    
   Serial.flush();            //Needed otherwise the sending on serial1 will effect reading info on serial2, flush makes the contorller pause until its done sending
   delay(100);
  
  
  }
  
void reset(byte ID){
  byte buf[] = {ID,0x02,0x06};
  memcpy ( sendingData, buf, sizeof(buf) );  //sizeof(buf)
  sendInformation(sendingData, sizeof(buf));
  }
  
int ping(byte ID){
  byte buf[] = {ID,0x02,0x01};
  memcpy ( sendingData, buf, sizeof(buf) );  //sizeof(buf)
  sendInformation(sendingData, sizeof(buf));
  getInfo();
  return (returningData[4]);
  }
  
void setIDtoAll(int value){
  //if(checkIsBetweenValue(value,0, 1)){
  byte buf[] = {0xFE,0x04,0x03,0x03,value};
  memcpy ( sendingData, buf, sizeof(buf) );  //sizeof(buf)
  sendInformation(sendingData, sizeof(buf));
  //}
}


void limitReturnPackage(byte ID, int value){
  byte buf[] = {ID,0x04,0x03,0x10,value};
  memcpy ( sendingData, buf, sizeof(buf) );  //sizeof(buf)
  sendInformation(sendingData, sizeof(buf));
  }


int getCurrPos(){
  byte buf[] = {currID,0x04,0x02,0x24,0x02};
  memcpy ( sendingData, buf, sizeof(buf) );  //sizeof(buf)
  sendInformation(sendingData, sizeof(buf));
  getInfo();
  return (returningData[5]+returningData[6]*255);
  }


int getCurrSpeed(){
  byte buf[] = {currID,0x04,0x02,0x26,0x02};
  memcpy ( sendingData, buf, sizeof(buf) );  //sizeof(buf)
  sendInformation(sendingData, sizeof(buf));
  getInfo();
  return ((returningData[5]+returningData[6]*255));
  }
  
int getSetSpeed(){
  byte buf[] = {currID,0x04,0x02,0x20,0x02};
  memcpy ( sendingData, buf, sizeof(buf) );  //sizeof(buf)
  sendInformation(sendingData, sizeof(buf));
  getInfo();
  return ((returningData[5]+returningData[6]*255));
  }
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
